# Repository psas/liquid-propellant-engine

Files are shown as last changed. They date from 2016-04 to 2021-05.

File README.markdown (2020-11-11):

# PSAS Liquid-Propellant Engine (LPE) Designs

## Overview

PSAS is building a LPE because (1) it's cool and (2) it's part of our 100 km rocket project. This project started with a 2015-2016 ME capstone of a 2kN 1/4 scale engine and is building towards a planned 9 kN engine for the LV-4 vehicle.

## Latest information

## 2020-2021 creation of the 2kN heat sink engine

Regenerative cooling is hard, particularly when we don't know if the basic engine design is viable. For this reason (and because we already bought some expensive parts), we are moving back to a ~2kN preliminary design. In various documents, this engine may be referred to as:

* 2kN Heat Sink Engine
* Minimum Viable Produce (MVP) engine
* Test Stand Demonstration Engine

The engine is intended to fire for no more than several seconds on the PSAS test stand. The hope is this engine will provide validation for the rocket design, manufacturing learnings and provide experience with a full-up hot fire test.

[Documentation for this engine](https://github.com/psas/liquid-propellant-engine/tree/master/2kN%20Heat%20Sink%20Engine)

## 2019-2020 Test Stand/Engine ME Capstone

Designed a 6kN heat sink engine... and then found out it was going to be too expensive to print and destroy this engine. Recommending moving back to 2kN for cost purposes.

[6kN Heat Sink Engine](https://github.com/psas/liquid-propellant-engine/tree/master/6kN%20Heat%20Sink%20Engine)

## 2018-2019 Test Stand Integration MME capstone

Project files analyzing and machining the 500lbf thrust printed engine.

Quick links to folders:
* [CT scanning](https://github.com/psas/liquid-propellant-engine/tree/master/2kN/CT%20scanning) <br>
* [Machining](https://github.com/psas/liquid-propellant-engine/tree/master/2kN/Machining)

## 2015-2016 liquid engine MME capstone.

Project files to develop a 500 lbf thrust 3D-printed liquid fuel rocket engine with LOX and IPA propellants. Here are a few helpful links:

* [Combustion chamber design Jupyter notebook](https://nbviewer.jupyter.org/github/psas/liquid-engine-capstone-2015/blob/master/2kN/analysis/Jupyter_Notebooks/LFRE.ipynb)
* [Pintle injector design Jupyter notebook](https://nbviewer.jupyter.org/github/psas/liquid-engine-capstone-2015/blob/master/2kN/analysis/Jupyter_Notebooks/Pintle%20Injector.ipynb)
* [Sketchfab 3D model of the Rev. 1 engine](https://sketchfab.com/models/ce8a3ff7d1e2417f9e614df5d085f7b0)
* [A short AIAA Space 2016 proceedings paper discussing the engine concept](https://github.com/psas/liquid-engine-capstone-2015/blob/master/2kN/doc/AIAA%20Space%20Proceedings/AIAA_Space_2016_Proceedings__LFRE_.pdf)
* [A short document explaning how the parametric curves for the cooling channels are computed](https://github.com/psas/liquid-engine-capstone-2015/blob/master/2kN/doc/Nozzle_Construction_docs/Cooling_Channel_Geometry_complete.pdf)

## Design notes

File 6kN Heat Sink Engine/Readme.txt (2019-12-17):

This is the location for 2019-2020 heat sink engine work.

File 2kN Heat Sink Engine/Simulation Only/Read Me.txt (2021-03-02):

This folder contains files that are to be used for optimizing the injector only. Dimensions may not match the current version. Dimensions that are directly relevant to the flow through the injector are the only parameters that should be updated to the current version.

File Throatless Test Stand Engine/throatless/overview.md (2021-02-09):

# Overview
This model is an estimated replica of Copenhagen Suborbital's BPM2. The model's dimensions are rough estimates from visually guessing BPM2's size in videos. The simulations were conducted with Solidworks Flow Sim. Inlet boundary conditions were gaseous H2O, 3000K, 250psi, with varying mass flow rates. Outlet boundary condition was environmental opening at 14.7psi and 293.15K temperature.

### My findngs

From Rocket Propulsion Elements by Sutton, Chapter 3.2:
> Chamber velocity can only be neglected if Ac/At > 4, only if chamber cross sectional area is 4 times bigger than throat area.

I believe that the losses from a throatless engine come from the immediate pressure loss in the chamber which is why the gas in the chamber is already accelerated and not stagnant like a traditional rocket engine. The high gas velocity right at the injector may be a result of the pressure loss, due to chamber and lack of throat geometry, which is being converted to velocity. 

Author: Kabir Bajwa

Date: February 9, 2021

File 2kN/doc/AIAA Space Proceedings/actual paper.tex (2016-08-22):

\typeout{}\typeout{If latex fails to find aiaa-tc, read the README file!}
%

\documentclass[]{aiaa-tc}% insert '[draft]' option to show overfull boxes
\usepackage{subfigure}
\usepackage{url}

 \title{Development of a Small Bipropellant Rocket Engine Utilizing Additive Manufacturing Processes}

 \author{
  John Tucker%
    \thanks{Student, Maseeh College of Engineering, AIAA Student Member.}
    \ Tamara Dib\thanksibid{1}\
  \ Taylor Rice\thanks{Student, Maseeh College of Engineering, AIAA Member}\ 
  \ Erin Schmidt\thanksibid{1}\
  \ Kristin Travis\thanksibid{1}\\
  \and
  \ and Bianca Viggiano%
   \thanks{Student, Maseeh College of Engineering.}\\
  {\normalsize\itshape
 Portland State University, Portland, OR, 97201, United States}
 }
 
 \AIAApapernumber{YEAR-NUMBER}
 \AIAAconference{AIAA SPACE 2016, 13-16 September 2016, Long Beach, California}
 \AIAAcopyright{\AIAAcopyrightD{2016}}

 % Define commands to assure consistent treatment throughout document
 \newcommand{\eqnref}[1]{(\ref{#1})}
 \newcommand{\class}[1]{\texttt{#1}}
 \newcommand{\package}[1]{\texttt{#1}}
 \newcommand{\file}[1]{\texttt{#1}}
 \newcommand{\BibTeX}{\textsc{Bib}\TeX}

\begin{document}

\maketitle

\begin{abstract}
The complexity and cost of building a liquid fuel rocket engine typically makes such devices unobtainable for a majority of parties interested in their construction. Until recently, manufacturing processes and techniques limited the geometries available to the designer and rendered such engines cost prohibitive as options for inexpensive orbital space flight. Advances in additive manufacturing technologies provide the potential to prototype complex geometries on a lower budget and with lead times which would be considered unobtainable with traditional manufacturing methods. Furthermore, bipropellant liquid fuels offer many complex engineering considerations; the full analysis of which may not be within the design ability of many amateur builds. It is therefore advantageous to develop techniques for additive manufacturing rapid prototyping to make the study of bipropellant fuels more accessible. A mechanical engineering senior capstone team at Portland State University developed an open-source method for quickly prototyping small bipropellant liquid fuel rocket engines with regenerative and film cooling using additive manufacturing.
\end{abstract}

\section*{Nomenclature} %keeping dummy variables for guidance

\begin{tabbing}
  XXXXX \= \kill% this line sets tab stop
  $PSAS$ \> Portland State Aerospace Society\\
  $DMLS$ \> Direct Metal Laser Sintering\\
  $LFRE$ \> Liquid Fuel Rocket Engine\\
  $LOX$ \> Liquid Oxygen\\
  $AM$ \> Additive Manufacturing\\
  $BF$ \> Blockage Factor\\
  $TMR$ \> Total Momentum Ratio\\
  
 % $\Delta x$ \> Variable displacement vector \\
 % $\alpha$ \> Acceleration, m/s\textsuperscript{2} \\[5pt]
 % \textit{Subscript}\\
 % $i$ \> Variable number \\
 \end{tabbing}

\section{Introduction}
The Portland State Aerospace Society (PSAS) is an engineering student group dedicated to low-cost, open-source technology development for high powered rockets and avionics systems \cite{PSAS}. The stated long term goal of the group is to place a 1 $kg$ CubeSat into low Earth orbit with their own launch vehicle. One step needed to achieve this goal is to transition the current rocket design from a solid to liquid fuel engine. Explored herein is the process of designing and testing a 500 $lbf$ thrust engine using liquid oxygen (LOX) and ethanol as propellants with regenerative cooling channels, film cooling, and a pintle injector. The design process is documented using Python in Jupyter notebooks and shared using Github \cite{git}. The authors feel that open standards for space systems hardware and design will be of increasing importance to the nascent `new space' industry. In this context, and in the interest of empowering `citizen scientists' and raising the level of public discussion on the issue of low-cost access to space the (non-ITAR controlled), project deliverables are being made freely and publicly available under a GNU GPL v3.0 open-source licence. 

A Jupyter Notebook is a sharable web application which allows for the live execution of code, namely Python. Jupyter notebooks were utilized in order to create a development process for the design of a regeneratively and film cooled liquid fuel rocket engine. The Jupyter Notebook forms a template for regeneratively cooled chamber design. As design inputs are changed in the notebook, parametric curves, which form the basis of the geometry file for 3D printing, are generated appropriately. This allows for quicker development of geometry files for additive manufacturing and thus quicker lead times on engine prototyping. As additive manufacturing technology progresses and becomes widely accepted by industry, its capability in rocket component design needs to be further studied and understood. Alloys used in Direct Metal Laser Sintering (DMLS) have different strength, heat transfer, and surface roughness properties. This project aims to gain insights on these properties and 3D printed combustion chamber performance. 

% it would appear we've covered everything without a top level design section, should we move things out of engine? or will this be sufficient?

%\section{Top Level Design}

\section{Engine}

%make the table a sub section? Also, i have zero clue about the style guide for a table, so I'm just going to construct it, with as much information as possible, we can cut or add anything we want, and style it all at once. I've commented out a lot of engine parameters, if you want to include them just uncomment them.

Engine design is typically cost prohibitive for many amateur designers who may be able to contribute to the advancement of low cost orbital space flight. The design process is cumbersome, and oftentimes does not result in a final product that will successfully fire due to the complexity of engine design. Engineering tools are not generally available, and an understanding of the full process is lacking. Due to the aforementioned constraints, it is desirable for the amateur to have available a design tool which will aid in generating a geometry capable of withstanding the stresses of a steady-state engine, while simultaneously producing a desired thrust. A production engine was generated and built using the Jupyter Notebook. Table \ref{tab:engineparams} shows a variety of the theoretical engine parameters generated by the liquid fuel rocket engine (LFRE) notebook.

\begin{table}
\begin{center}
\begin{tabular}{| l | c | c |}

\hline
 Parameter, variable                      & Unit     & Value     \\
 \hline
 Nozzle force, $F$                        & $lbf$       & 500       \\
 O/F weight mixture ratio, $r_w$          & --  & 1.2       \\
 Fuel mixture percentage, $r_{w_{fuel}}$  & --   & 0.595      \\
 Contraction ratio, $\varepsilon_c$       & --  & 10.5      \\
 Ratio of specific heats, $\gamma$        & --  & 1.12      \\

 %Pressures:
 Total chamber pressure, $P_{c_{inj}}$    & $psi$  & 350.00    \\
 Throat pressure, $P_t$                   & $psi$       & 202.73    \\

 %Velocities:
 Throat velocity, $V_t$                   & ${ft}/{s}$    & 3464.05   \\
 Exit velocity, $V_e$                     & ${ft}/{s}$    & 7804.45   \\

 %Mass Flow Rates:
 Total mass flow rate, $\dot w$           & ${lb}/{s}$    & 2.06      \\

 %Temperatures:
 Stagnation temperature, $T_{c_{ns}}$             & $^\circ R$ & 5487.10   \\
 Adiabatic wall temperature at inlet, $T_{awi}$   & $^\circ R$ & 4389.64   \\
 Adiabatic wall temperature at throat, $T_{awt}$  & $^\circ R$ & 4379.47   \\

 Specific Impulse, $I_s $                 & ${lb\cdot s}/{lb}$    & 242.37    \\
 Characteristic velocity, $c*$            & ${ft}/{s}$            & 5325.59   \\

 Chamber volume, $V_c$                    & $in^3$      & 27.35     \\
 Chamber cross sectional area, $A_c$      & $in^2$      & 10.26     \\
 Throat radius, $r_t$                     & $in$        & 0.558     \\
 Exit radius, $r_e$                       & $in$        & 1.037     \\
 Wall thickness, $t$                      & $in$        & 0.01820   \\
 
 Cooling channel base width at throat, $b_t$              & $in$        & 0.02522   \\
 Cooling channel base width at exit, $b_e$                & $in$        & 0.06192   \\
 Cooling channel effective radius at throat, $r_{cch_t}$  & $in$        & 0.01261   \\
 Cooling channel effective radius at exit, $r_{cch_e}$    & $in$        & 0.03096   \\
 Cooling channel hydraulic diameter, $d$                  & $in$        & 0.04671   \\
 Cooling channel total area, $A_c$                        & $in^2$      & 1.16537   \\
 Number of cooling channels, $n$                          & --  & 82        \\

 Coolant side heat transfer coefficient, $h_c$    & ${Btu}/({in^2\cdot s\cdot^{\circ}F})$   & 0.15609   \\
 Required heat flux, $\dot q$                          & ${Btu}/({in^2\cdot s})$                 & 27.72     \\
 Coolant capacity, $Q_c$                          & ${Btu}/{s}$                           & 341.68    \\
 
 Combined tangential stress at nozzle exit, $S_{t_e}$     & $psi$       & 32224.43  \\
 Combined tangential stress at throat, $S_{t_t}$          & $psi$       & 31554.40  \\
\hline
\end{tabular}
\end{center}
\caption{Parameters obtained from the Jupyter Notebook for the production engine chamber and nozzle design.}
\label{tab:engineparams}
\end{table}

The LFRE Nozzle Jupyter Notebook \cite{LFRE} allows the user to input desired design requirements; namely thrust and material properties, to subsequently aid the designer in generating an acceptable geometry for the specified requirements. NASA's CEARUN tool \cite{CEARUN} is used to generate many of the initial design parameters as inputs. Certain design constraints (fuel combination, mixture ratio, and chamber pressure) must be known prior to utilizing the CEARUN tool, and should be selected according to needs of the engine design. After inputs are provided, the basic geometry of the nozzle is determined. Furthermore, the analysis determines the cooling capacity of the fuel used in regenerative passages resulting in parametric equations which describe the chamber and nozzle contours, the inner and outer surfaces of the regenerative cooling passages, and the external surface of the nozzle. The parametric equations may then be used to generate a printable 3D model in combination with additive manufacturing processes.

The regenerative cooling passages constructed using the parametric equations are of uniform cross-sectional area normal to the surface of the nozzle contour. These parametric equations were derived in order to mathematically define a nozzle contour and its various cooling channel geometries in general such that no geometry would have to be calculated by the designer, and a nozzle could be generated by virtue of only the geometric parameters which make it unique \cite{parametricEQs}. Full development of the parametric equations are available for inspection, but are not provided here for the sake of brevity. This allows the  cross sectional area to be scaled as a means of controlling the velocity of the fuel in a particular regenerative passageway, enabling better control of wall temperatures at any given axial position along the nozzle. Scaling functions may be added as a design tool at a later date, but initial functions resemble a half period of a sine function to scale along a desired length of nozzle in order to give a smooth and continuous scaling pattern along a given section of the nozzle. Because the nozzle is parametrized, any parametric equation justifying a nozzle section may simply be multiplied by a scaling function in order to more directly control cooling over specific areas of the nozzle.
 
After generating parametric equations, a more detailed heat transfer analysis is undertaken. Properties are evaluated along finite sections of the wall contour, and compared to the capacity of the specified coolant, to allow the designer to analyze if a particular nozzle geometry is capable of reaching a thermal equilibrium while remaining below the thermal and mechanical stress limits of the engine material and the boiling point of the fluid. The analysis generates graphs of several key properties along the nozzle contour as shown in figure \ref{fig:propertygraphs}. The major outputs of the Jupyter Notebook are a unique set of parametric equations with which a liquid fuel rocket engine is created which utilizes regenerative and film cooling to protect the engine material from yield due to thermal and mechanical stresses during thermally steady state combustion.

%\begin{figure}[h]
%\centering
%   {\includegraphics[width=.3\textwidth]{graphs/radius_v_position.png}
%    \includegraphics[width=.3\textwidth]{graphs/mach_v_position.png}
%    \includegraphics[width=.3\textwidth]{graphs/pressure_v_position.png}
%    \includegraphics[width=.3\textwidth]{graphs/temp_v_position.png}
 %   \includegraphics[width=.3\textwidth]{graphs/velocity_v_position.png}
 %   \includegraphics[width=.3\textwidth]{graphs/HT_coeff_v_position.png}
 %   \includegraphics[width=.3\textwidth]{graphs/adiab_wall_temp_v_position.png%}
 %   \includegraphics[width=.3\textwidth]{graphs/heat_flux_v_position.png}}
 %   \caption{LFRE Jupyter Notebook sample output for various properties along the length of the developed nozzle}
 %%   \label{fig:propertygraphs}
%\end{figure}

\begin{figure}[ht]
\centering
   {
    
    }
    \caption{LFRE Jupyter Notebook sample output for Mach number, temperature and heat flux along the length of the developed nozzle. For a complete set of parameters plotted as a function of nozzle position see the Github repo \cite{LFRE}.}
    \label{fig:propertygraphs}
\end{figure}

Correction factors are implemented into the Jupyter Notebook to address discrepancies between theoretical values for various parameters and their empirically tested values. The primary correction factor to be addressed after testing an engineering prototype should be the adiabatic wall temperature of the hot exhaust gas due to film cooling. Models for film cooling are not well established, and it is important to determine a correction factor for a particular engine in order to accurately predict the resulting physical properties of subsequent iterations of engine prototypes. This will allow a designer to predict the flow rates and pressure drops of propellants with enough accuracy to design a propellant feed system capable of delivering required pressure to an engine without the need to iterate through many costly test stand designs.

\subsection*{Engine Features}

The first engine prototype shown in figure \ref{fig:nozzlecross} is intended to produce 500 $lbf$. It is produced by a DMLS 3D printing process and made from high temperature aluminum alloy, AlSI10Mg. External to this project, a test stand  is being built that is capable of delivering fuel at approximately 500 $psi$ to the fuel manifold, which is located at the base of the nozzle bell. Upon collection, the fuel is directed through regenerative cooling channels. The fuel is then delivered to a collection chamber. Care should be taken to limit the overhang angles within the larger geometries of the collection chamber. This limit is dictated by the particular 3D printing process which is being utilized. The designer should consider the print orientation and maximum overhang angle. The presented prototype was printed with a maximum overhang angle of 45$^\circ$, and the design resulted in minimal use of support material. Upon collection, the fuel is directed to film cooling ports, shown in figure \ref{fig:designcross}; of which the size and quantity are optimized by the Jupyter Notebook. Remaining fuel is then utilized as propellant, which is directed around a pintle injector, described in section \ref{sec:PI}. After injection and combustion occur, the propellants are directed through a de Laval nozzle design based on Rao's parabolic bell approximation \cite{rao1961recent}.

\begin{figure}[ht]
\centering
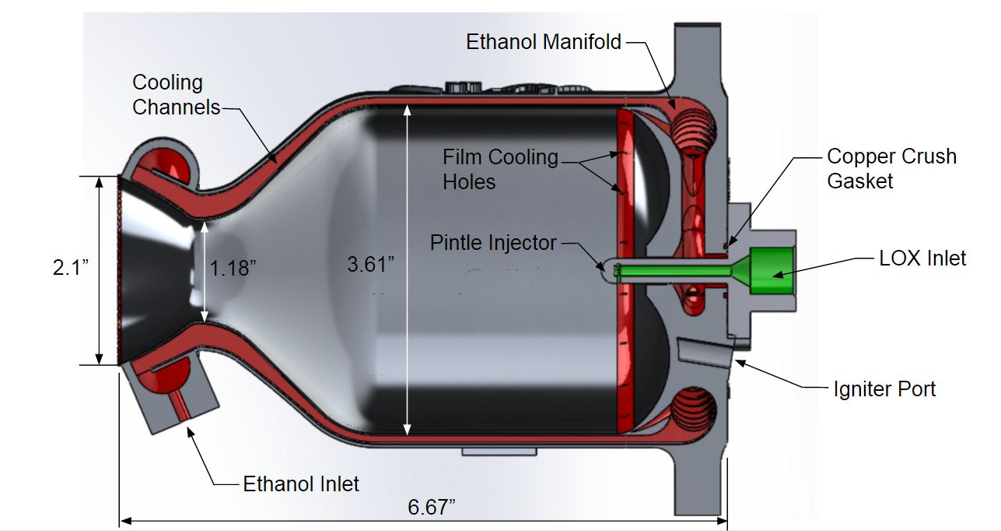
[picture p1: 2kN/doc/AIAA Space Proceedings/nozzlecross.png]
   {}
    \caption{Final assembly cross section drawing of the rocket engine. Areas in red show the regenerative cooling channels and the path the fuel takes through the engine. Areas in green are the liquid oxygen flow path.}
    \label{fig:nozzlecross}
\end{figure}

\begin{figure}[ht!]
\centering
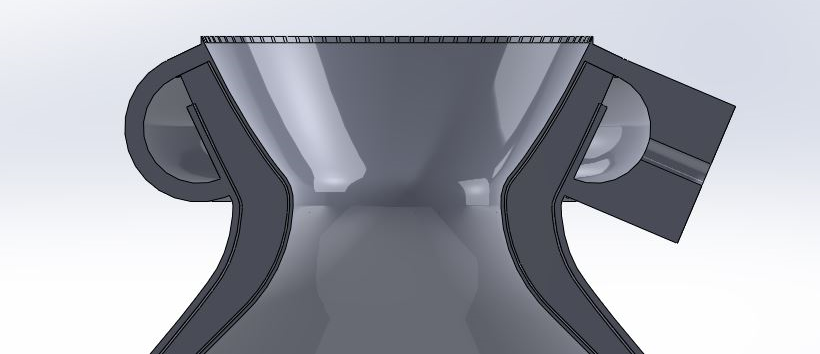
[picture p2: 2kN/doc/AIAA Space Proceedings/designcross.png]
    {}
    \caption{Final design cross section drawing of the nozzle bell, the nozzle and fuel manifolds are manufactured as a single part. The nozzle is a parabolic approximation of a de Laval converging-diverging nozzle.}
    \label{fig:designcross}
\end{figure}

DMLS uses high energy pulse CO2 lasers (carbon dioxide laser) to fuse metal particles together, layer-by-layer, to form a solid product. The process is done in a powder bed that inherently provides support material for any overhanging features. Because of this, complex features and internal passageways are possible utilizing DMLS that are not possible with traditional machining approaches. Incorporating DMLS manufacturing allows the designer to work towards the 'ideal' design for a rocket engine without the added burden of considering machinability. Features such as regenerative cooling channels no longer require special machining strategies for incorporation into a design. They are instead printed directly into the nozzle contours simply and accurately with only feature size and overhang angles as constraints. 

\section{Pintle Injector}
\label{sec:PI}

%The pintle section needs a stats table, similar to the engine stats table. 
%Here it is, but it needs formatting

There are several possibilities for the selection of the injector.
%This sentence doesn't make sense to me. Are 'stable and efficient manners' performance characteristics? Which performance characteristics?
%Most injector types are capable of atomizing the fuel in a stable and efficient manner, therefore performance characteristics are not the driving factor in design selection.
A 500 $lbf$ thrust engine has low fuel mixing requirements; as long as the mass flow rates and momentum ratios are satisfied, many different designs will suffice. Swirl injectors, as well as impinging jet injectors were considered; however, these designs are more complex and potentially more difficult to integrate with 3D printed cooling channels. As a result, an interchangeable pintle injector design based on 
research published by Santoro was selected \cite{santoro1999main}. A pintle injector will be fixed to the engine via bolts or machine screws, making it relatively easy to remove and replace if alterations are necessary. Additionally, pintle injectors are less susceptible to combustion instabilities  and are potentially throttle-able; features that will benefit future PSAS liquid engine designs\cite{dressler2000trw}. 
%is it ok that I changed 'larger' to 'PSAS liquid'?

The pintle injector is responsible for delivering the liquid oxygen to the combustion chamber. 316 stainless steel was chosen as the pintle injector material because of its LOX compatibility and thermal resistance qualities. The liquid oxygen travels down the center of the pintle and leaves the LOX holes at a 90$^\circ$ angle to the original direction of travel. The liquid oxygen exiting the pintle holes collides with the annulus fuel stream and creates an atomized mixture. The oxygen holes and fuel gap have been sized to achieve near equal flow momentum of each propellant resulting in a TMR near unity to ensure the trajectory of the mixture inside the combustion chamber is $\sim$45$^\circ$. The design for the pintle injector is shown in figure \ref{fig:PIxsection}.

\begin{figure}
\centering
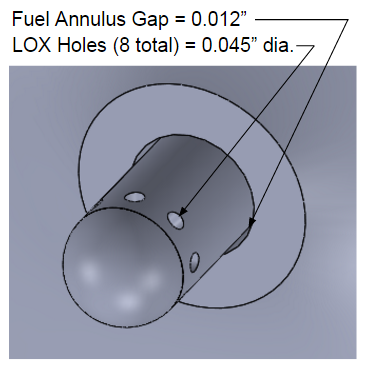
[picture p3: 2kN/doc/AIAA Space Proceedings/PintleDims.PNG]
   \subfigure[]{}
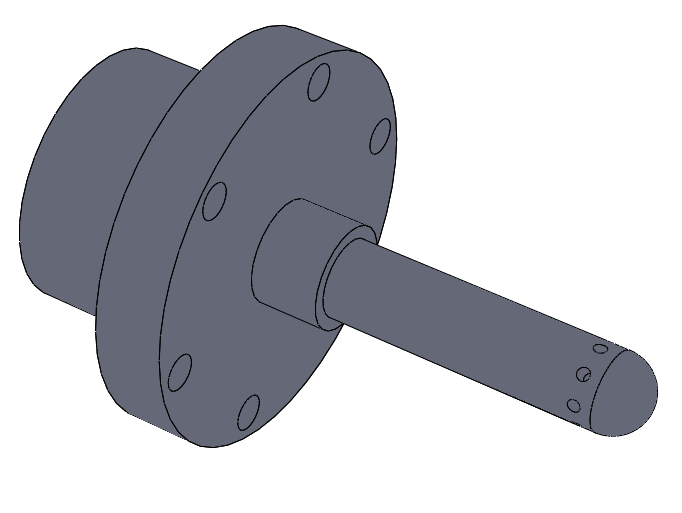
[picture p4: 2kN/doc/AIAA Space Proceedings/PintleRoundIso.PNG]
   \subfigure[]{}
    \caption{Pintle LOX holes and fuel annulus inside combustion chamber (a) and Stainless Steel pintle injector design (b).}
    \label{fig:PIxsection}
\end{figure}

Currently there is little published data on the design and construction of pintle injectors. Therefore an extensive documentation of the design process has been outlined in the Github repository. Using the Jupyter Notebook in Github, radii for the LOX holes and the fuel annulus were determined from inputs for required chamber pressure and propellant mass flow rates. The dimensions of the radii can be adjusted according to recommended blockage factor (BF) and total momentum ratio (TMR) values provided by Woodward \cite{woodward1998injector}. The notebook is constructed for ease in calculations for an iterative process. Table \ref{tab:pintle} shows the theoretical parameters generated by the Jupyter Notebook that pertain to the design of the current pintle injector.

\begin{table}
\begin{center}
\begin{tabular}{| l | c | c |}
\hline
 Parameter, variable                          & Unit     & Value     \\
  \hline
  Pintle center LOX flow rate, $\dot w_{ox}$                                  & ${lb}/{s}$       & 1.13       \\
   Outer annulus ethanol flow rate, $\dot w_f$
   & ${lb}/{s}$       & 0.94       \\
 Pintle outer radius, $R_p$                              & $in$       & 0.14       \\
 Pintle inner radius, $r$          
 & $in$   & 0.06       \\
Fuel annulus radius, $R_a$          
 & $in$   & 0.152       \\
 Annulus gap, $t$          
 & $in$   & 0.012       \\
 Injector pressure drop, $\Delta P$          
 & $psi$   & 70       \\
  Pintle hole diameter, $d_h$          
 & $in$   & 0.045       \\
   Number of pintle LOX holes, $N$         
 & --   & 8       \\
  Theoretical Blockage Factor, $BF$          
 & --   & 0.41       \\
   Theoretical Total Momentum Ratio, $TMR$          
 & --   & 0.97       \\  
\hline
\end{tabular}
\end{center}
\caption{Parameters obtained from the Jupyter Notebook for the current pintle injector design.}
\label{tab:pintle}

\end{table}

\section{Ongoing and Future Work}
All entities of the printed production engine, shown in figure \ref{fig:IMG_1371}, must still be tested, including the injector and nozzle. The regenerative cooling channels of the nozzle will be cold flow tested prior to any hot fires. The pintle injector has been designed and is in the midst of being machined; it will be cold flow tested prior to being attached to the nozzle. The ignition system is currently being designed as well as the instrumentation to test fire the engine.%'engine' used to be 'rocket'. 

\begin{figure}[ht!]
\centering
    {}
    \caption{Printed engine to be cold tested and hot fired.}
    \label{fig:IMG_1371}
\end{figure}

A future iteration of the Jupyter Notebook would include constant hydraulic diameter as an output rather than a constant cross sectional area, in order to give the designer a unit flow velocity along the channels. The flow velocity could then be scaled as desired around areas of high heat transfer such as the throat.

\section{Conclusion} %I am adddding a sentence here.
To the knowledge of the authors, no other open-source method for quickly prototyping liquid fuel engines exists. The first iteration of this engine will be tested on a test stand in 2016. The results obtained from the cold tests and hot fire of the engine will aid in future iterations and give insight into the validity of the equations utilized for this engine. 3D printed engines are just beginning to be developed and tested by industry, and few have been tested in flight. Additive manufacturing has opened the door for design innovation, low cost development, and amateur group access to space.

%\section*{Appendix}
%should we include links to things like the derivations of contour equations, or the various Jupyter notebooks?

\section*{Acknowledgments}
The authors are grateful to PSAS for funding and initiating this project, Faculty Advisor Dr. Derek Tretheway for his advice and guidance and Cam Yun for his work on the project. The authors are also grateful to Robert Watzlavick, David Gregory, and Armor Harris for their advice, and the Oregon Air National Guard for their guidance on LOX handling. Finally the authors are indebted to i3D MFG for their ongoing support with additive manufacturing and Machine Sciences Corporation for their support with traditional machining.

\bibliography{aiaabib}
\bibliographystyle{aiaa}

\end{document}

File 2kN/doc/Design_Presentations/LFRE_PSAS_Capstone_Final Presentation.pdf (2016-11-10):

# Liquid Fuel Rocket Engine

## Portland State Aerospace Society Senior Capstone Project

Tamara Dib, Taylor Rice, Kristin Travis,

## John Tucker, Bianca Viggiano, Cam Yun Faculty Advisor: Derek Tretheway

# Portland State Aerospace Society (PSAS)

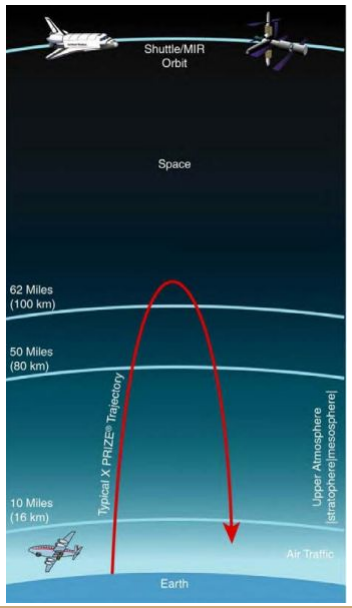
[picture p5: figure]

-University Space Race - The Von Karman Line (100km)

-Last Launch Altitude ~5km

-Transition from solid motor to liquid fuel engine to reach 100km

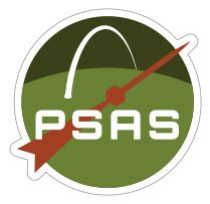
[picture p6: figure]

-Open Source - Github

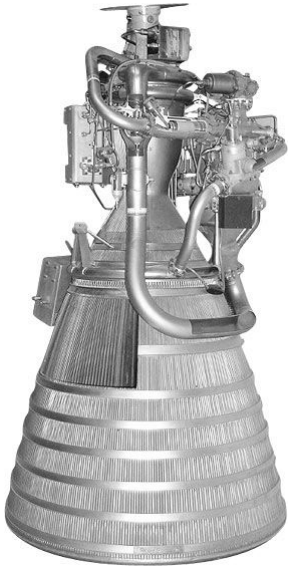
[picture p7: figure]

# Original Design Criteria

-Design, build and test a prototype static liquid fuel rocket engine with 50 lbf thrust capability

-Use DMLS additive manufacturing technology (3D-Print Direct Metal Laser Sintering)

-Scalable proof of concept design for future engine design iterations

-Develop and document engine design process to provide open source ‘templates’ for future engine designs

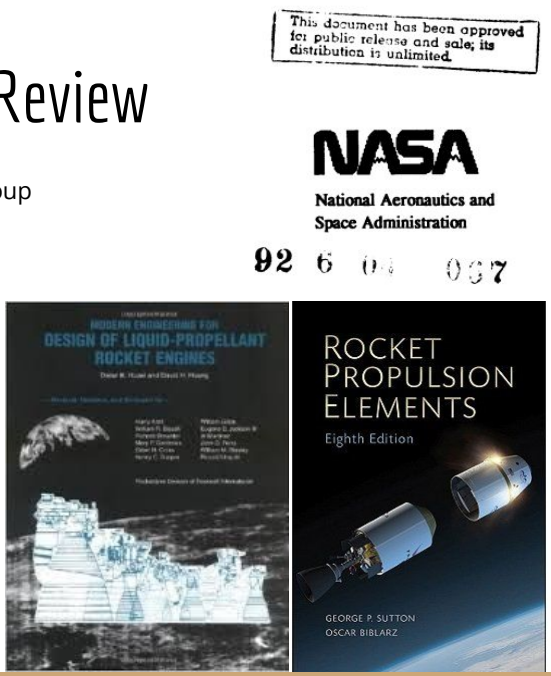
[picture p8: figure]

# External Search and Design Review

-Armor Harris - SpaceX and Boston University Rocket Group

-Robert Watzlavick - Aerospace Engineer

-Peter McCloud - Aerospace Engineer

-Oregon Air National Guard - LOX handling

-NASA and AIAA Publications

-aRocket - Amateur rocketry email list

-Reddit - Rocketry Thread

-Erin Schmidt - PSAS

# Current Engine Design

-500 lb Thrust

-Static test stand engine

-3D printed in Aluminum (AlSi10Mg)

-Ethanol and Liquid Oxygen (LOX) Propellants

-Fuel filled regenerative cooling channels

-Film cooling ports

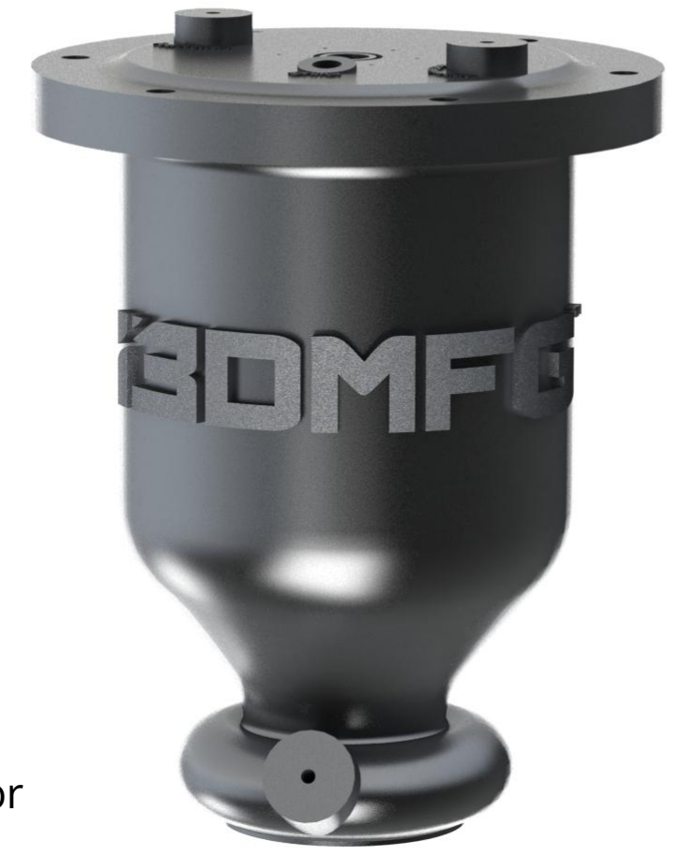
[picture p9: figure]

-LOX centered 316 stainless steel pintle injector

# Current Engine Design

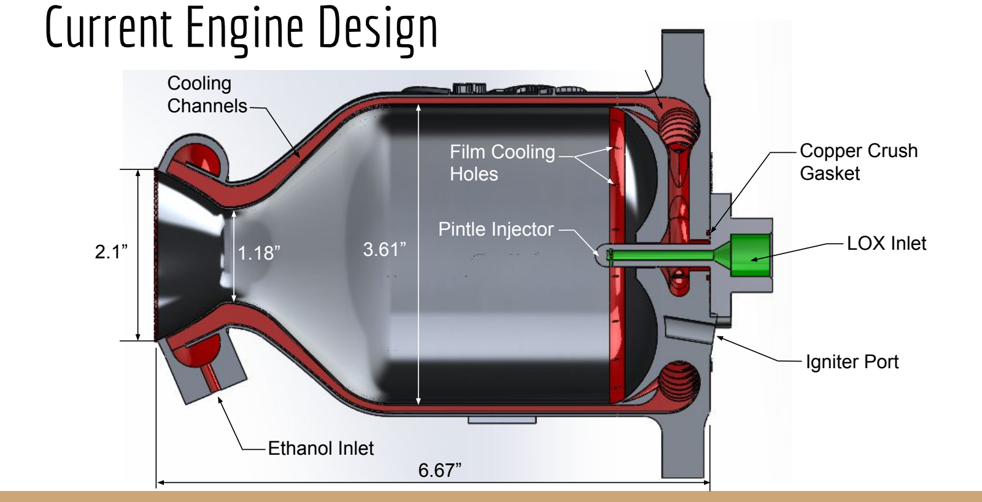
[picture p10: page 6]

Ethanol Inlet

Cooling
Channels

Ethanol Manifold

LOX Inlet

Copper Crush
Gasket

Pintle Injector
2.1” | 1.18” | 3.61”

6.67”

Film Cooling
Holes

Igniter Port

# Regenerative Cooling Channels

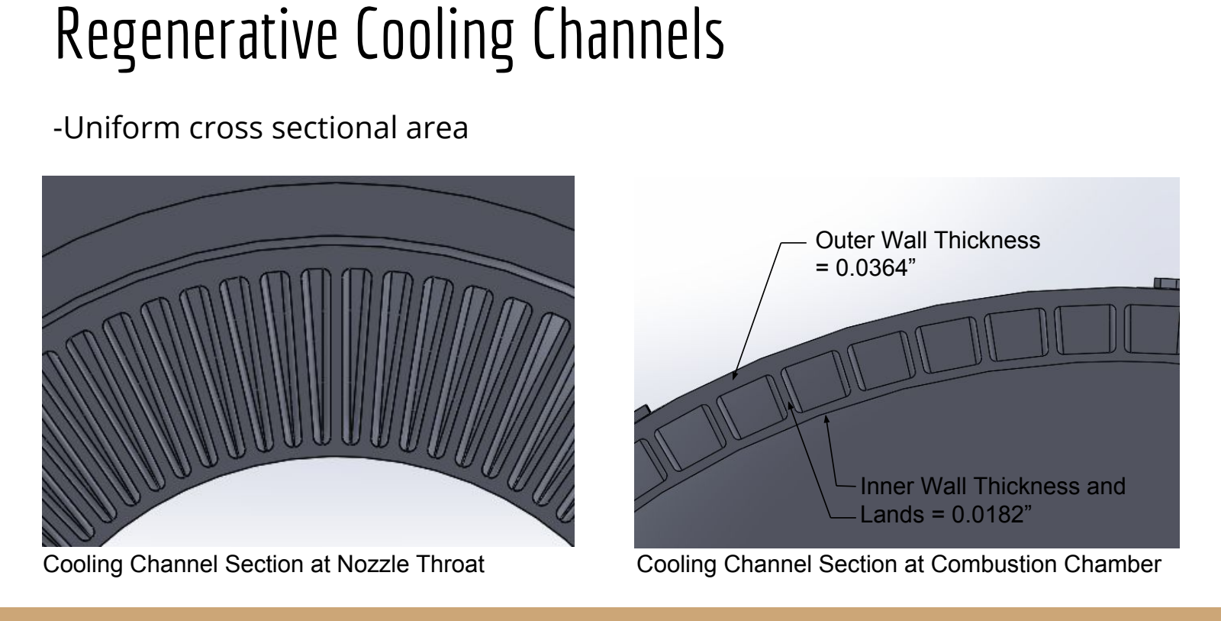
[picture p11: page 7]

Cooling Channel Section at Nozzle Throat | Cooling Channel Section at Combustion Chamber

-Uniform cross sectional area

Outer Wall Thickness
= 0.0364”

Inner Wall Thickness and
Lands = 0.0182”

# Heat Transfer Analysis and Film Cooling

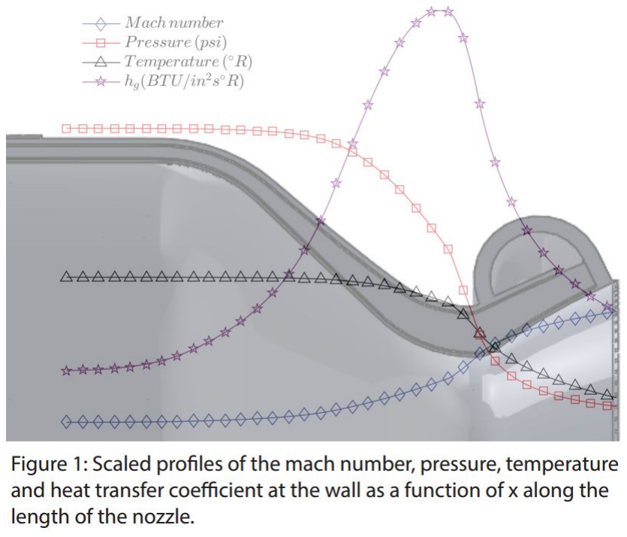
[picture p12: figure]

-Balance between thermal stresses
and print resolution

-Flow temperatures approaching 2,782 °C (5,500 °R)

# Open Source Jupyter (ipython) Design Notebooks

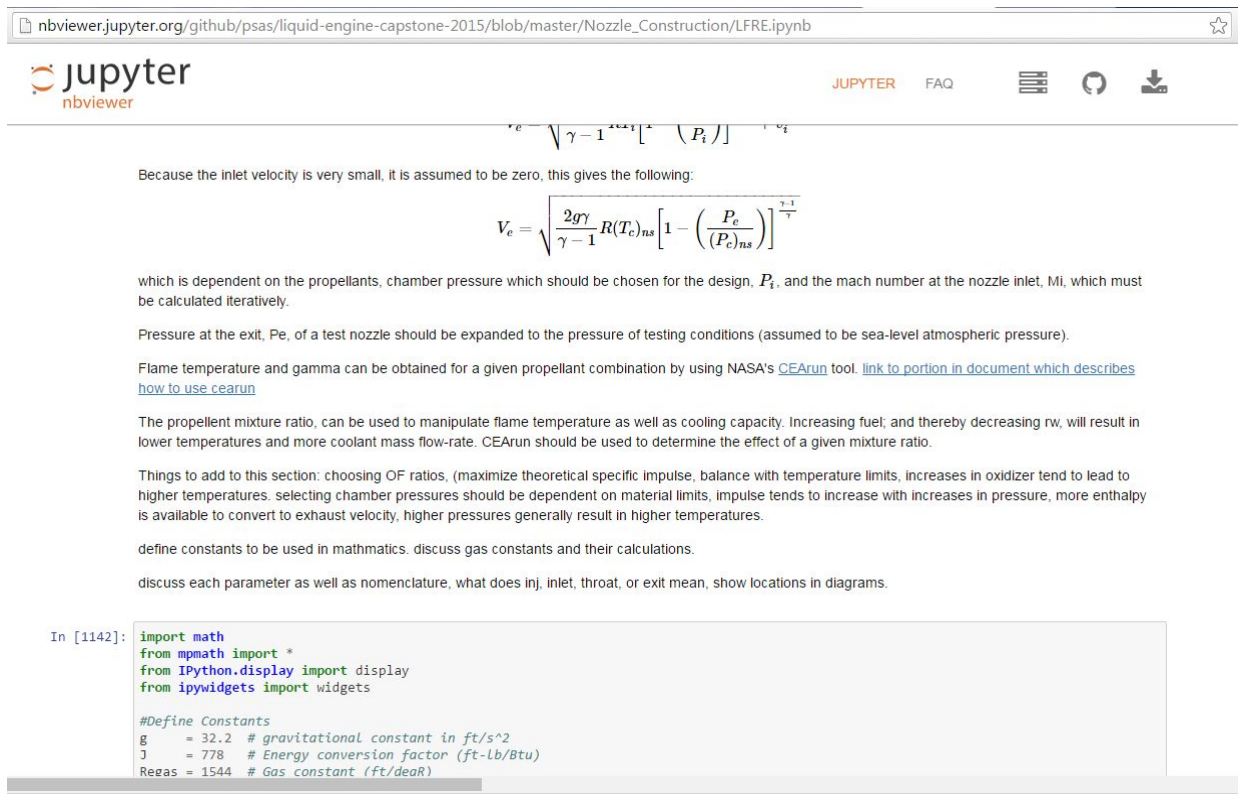
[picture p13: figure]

# Pintle Injectors

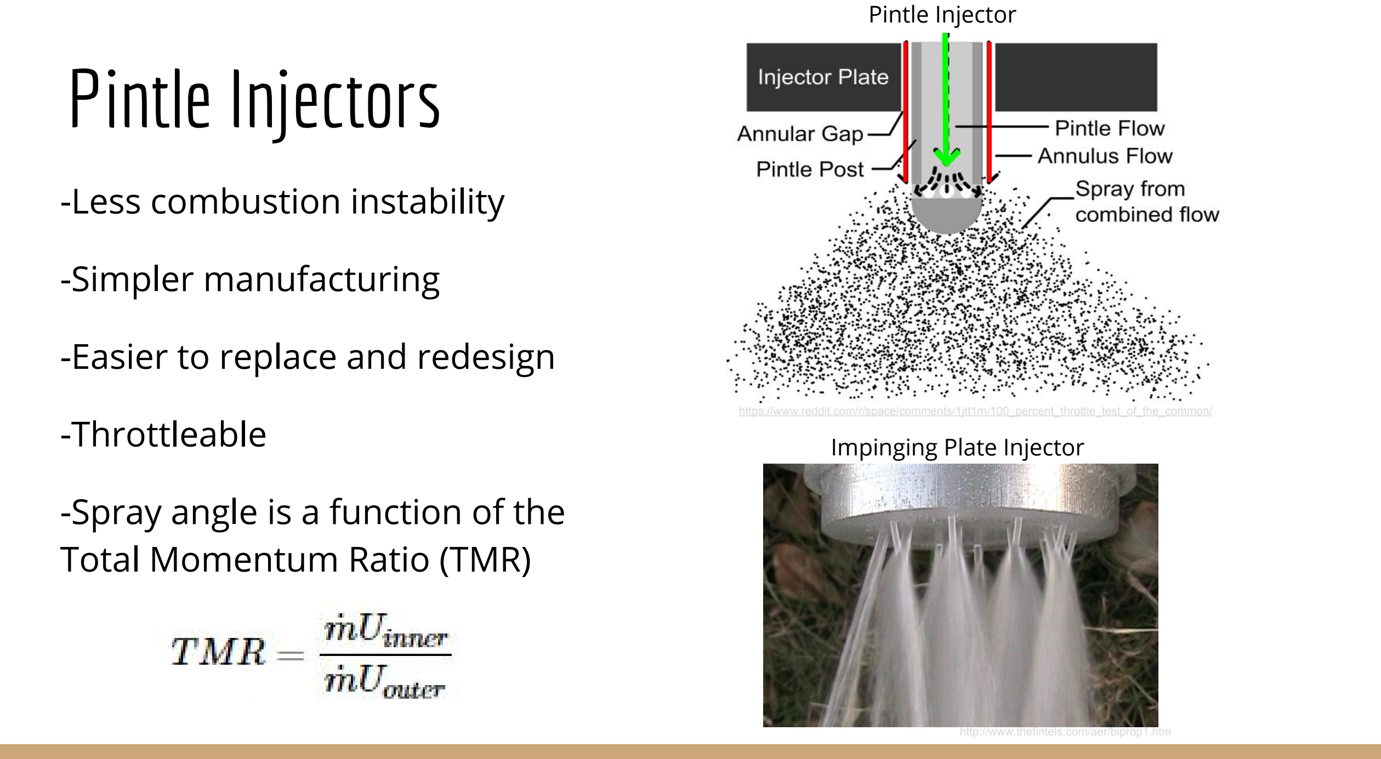
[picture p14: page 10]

-Less combustion instability

-Simpler manufacturing

-Easier to replace and redesign

-Throttleable

-Spray angle is a function of the Total Momentum Ratio (TMR)

Impinging Plate Injector

Pintle Injector

http://www.thefintels.com/aer/biprop1.htmhttps://www.reddit.com/r/space/comments/1jtt1m/100_percent_throttle_test_of_the_common/

# Pintle Injector Design

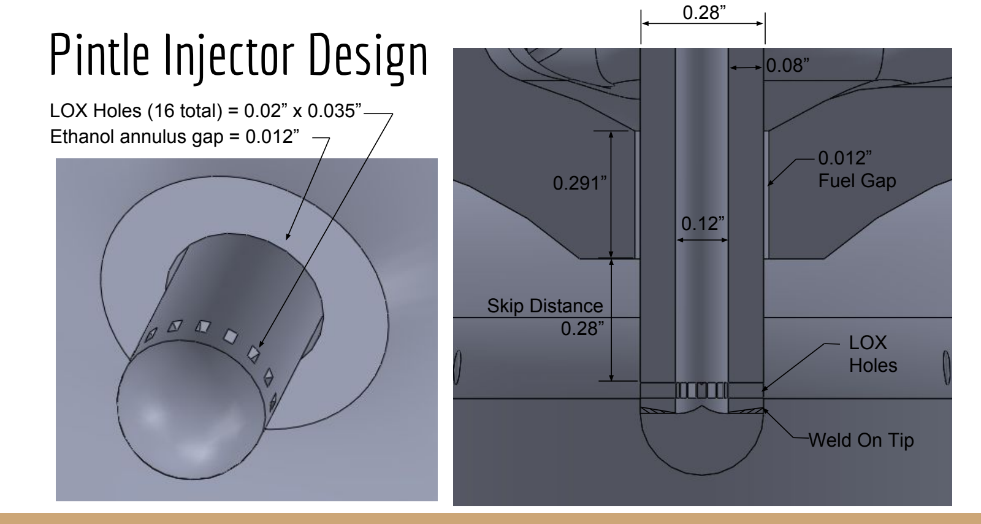
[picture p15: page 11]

0.28”

LOX Holes (16 total) = 0.02” x 0.035” Ethanol annulus gap = 0.012”

LOX
Holes

0.12”

Weld On Tip

0.291”

Skip Distance
0.28”

0.012”
Fuel Gap

0.08”

# Pintle Injector Design

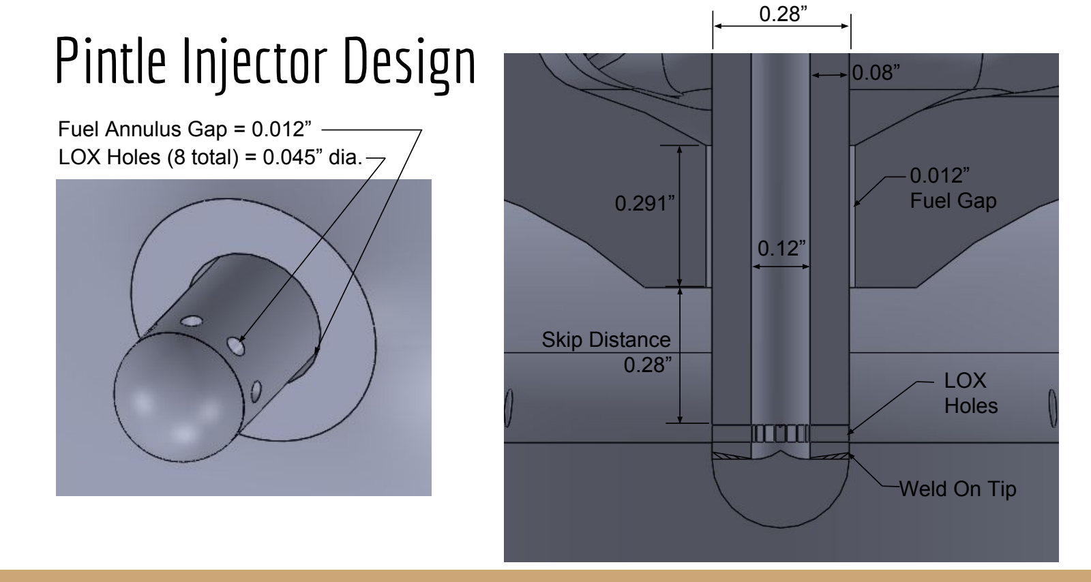
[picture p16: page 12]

0.28”

LOX Holes (8 total) = 0.045” dia.

Fuel Annulus Gap = 0.012”

LOX
Holes

0.12”

Weld On Tip

0.291”

Skip Distance
0.28”

0.012”
Fuel Gap

0.08”

# Torch Spark Igniter

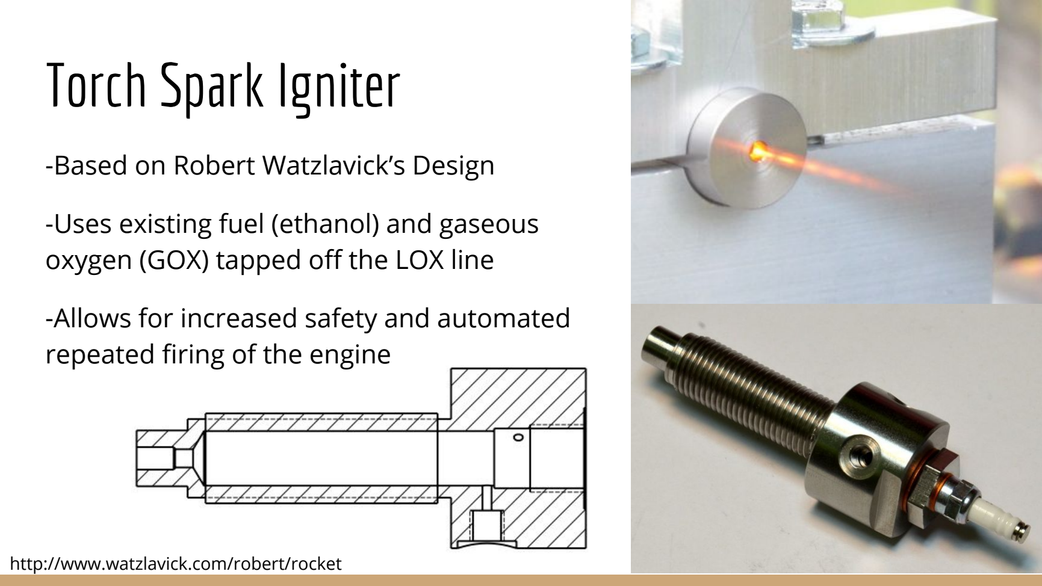
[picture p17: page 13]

-Based on Robert Watzlavick’s Design

-Uses existing fuel (ethanol) and gaseous oxygen (GOX) tapped off the LOX line

-Allows for increased safety and automated repeated firing of the engine

http://www.watzlavick.com/robert/rocket

# Liquid Oxygen (LOX) Handling

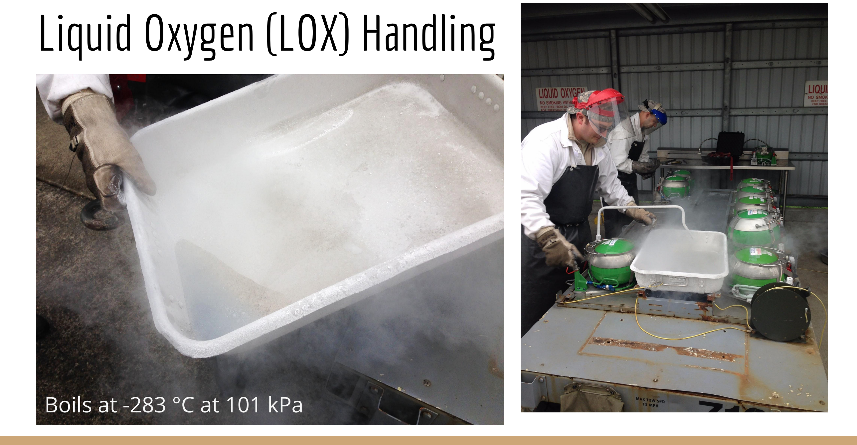
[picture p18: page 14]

Boils at -283 °C at 101 kPa

# Cool Images!

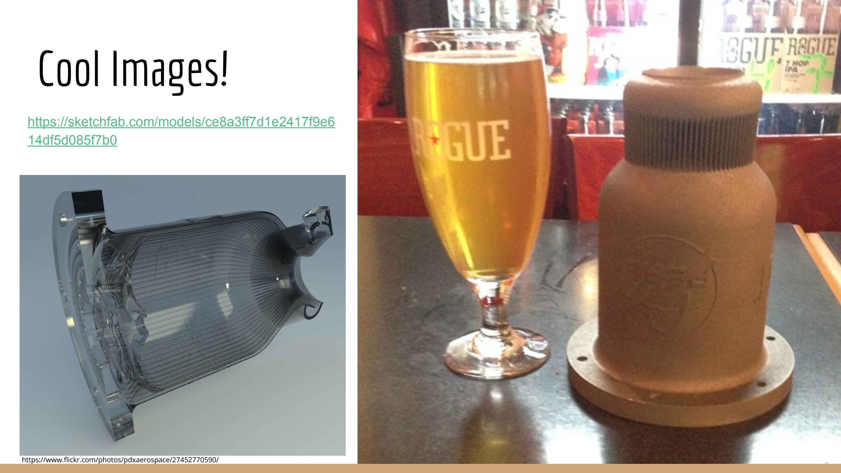
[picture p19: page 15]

https://sketchfab.com/models/ce8a3ff7d1e2417f9e6 14df5d085f7b0 (https://sketchfab.com/models/ce8a3ff7d1e2417f9e614df5d085f7b0)

https://www.flickr.com/photos/pdxaerospace/27452770590/

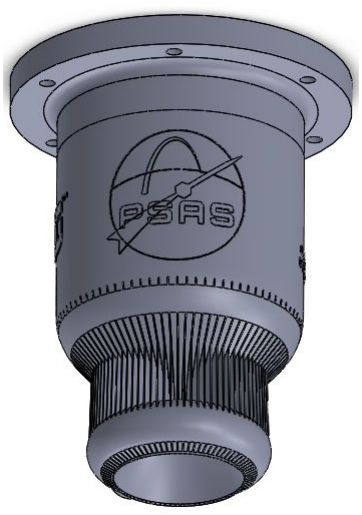
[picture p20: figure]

# Ongoing Projects

-Manufacture injector

-Cold flow test injector

-Test pressure loss in cooling channels

-Manufacture and test igniter

-FEA and CFD model validation

-Fire the Engine!

# Questions?

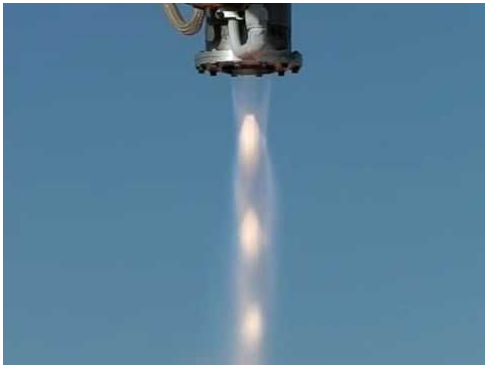
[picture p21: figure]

Thank you to all our supporters!

-i3D Manufacturing
-Portland State Aerospace Society -Derek Tretheway
-Andrew Greenberg
-Armor Harris
-Robert Watzlavick
-Peter McCloud
-Erin Schmidt

# Image References

http://psas.pdx.edu/
http://www.mrziegler.com/images/XPrizeTrajectory.jpghttps://www.asme.org/about-asme/who-we-are/engineering-history/landmarks/36-rl-10-rocket-enginehttp://i.imgur.com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
http://www.thefintels.com/aer/biprop1.htm
http://www.watzlavick.com/robert/rockethttps://www.flickr.com/photos/pdxaerospace/27452770590/https://i.ytimg.com/vi/KeGidtk6t2Y/hqdefault.jpg

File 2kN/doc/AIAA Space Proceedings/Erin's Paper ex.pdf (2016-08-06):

# Development of a Low-Cost, Open-Hardware Attitude Control System for High Powered

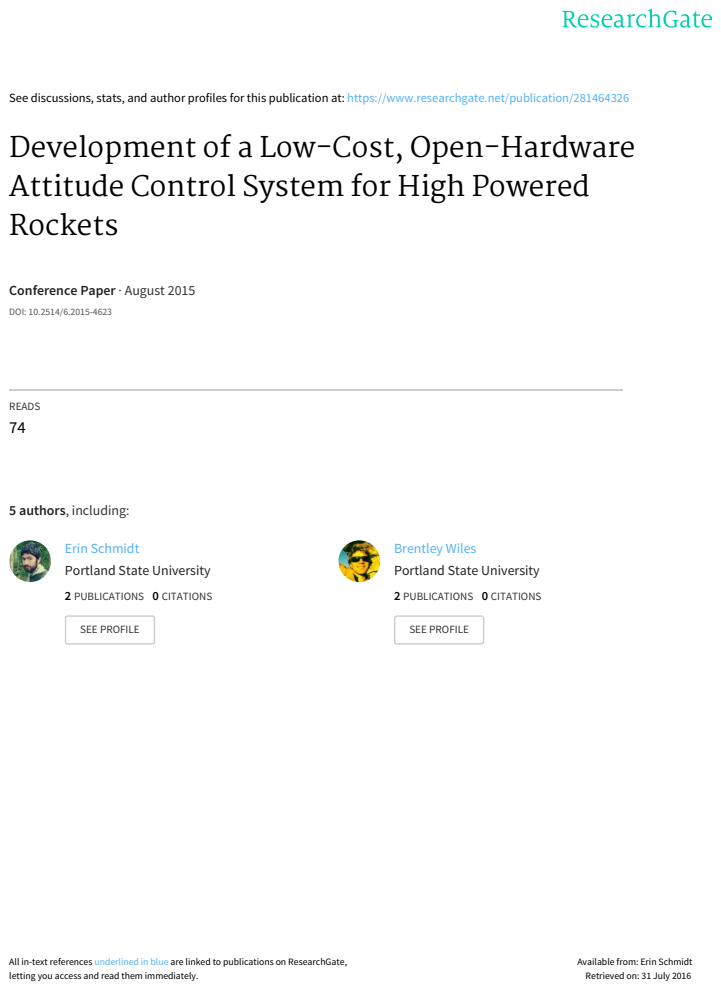
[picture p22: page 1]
Rockets; DOI: 10.2514/6.2015-4623; READS 74; 5 authors, including:; 2 PUBLICATIONS 0 CITATIONS; SEE PROFILE

See discussions, stats, and author profiles for this publication at: https://www.researchgate.net/publication/281464326

Conference Paper · August 2015

Erin Schmidt (https://www.researchgate.net/profile/Erin_Schmidt3?el=1_x_5)
Portland State University (https://www.researchgate.net/institution/Portland_State_University?el=1_x_6)

Brentley Wiles (https://www.researchgate.net/profile/Brentley_Wiles?el=1_x_5)

All in-text references underlined in blue are linked to publications on ResearchGate,
letting you access and read them immediately.

Available from: Erin Schmidt
Retrieved on: 31 July 2016

1 Student, Maseeh College of Engineering, Student Member 2 Student, Maseeh College of Engineering, Student Member 3 Student, Maseeh College of Engineering
4 Student, Maseeh College of Engineering, Student Member 5 Student, Maseeh College of Engineering, Student Member

American Institute of Aeronautics and Astronautics

# Development of a Low-Cost, Open-Hardware Attitude Control System for High-Powered Rockets

Erin Schmidt¹

, Jeremy Louke²

, Kenneth Arnell³

, Jeffrey Hickman⁴

, and Brentley Wiles⁵
Portland State University, Portland, OR 97201

Attitude control systems are an important enabling technology for amatuer and university class high-powered rockets to be more useful as platforms for high-altitude science, but are presently too costly and technically complex to implement for many groups. With the intention of making this technology more accessible to the high-powered rocketry field a mechanical engineering senior capstone team at Portland State University developed an open-source, scalable attitude control system leveraging COTS components, robust controls, and additive manufacturing. A qualitative narrative describing the system design process is presented here.

Nomenclature
COTS = Commercial Off The Shelf
DoF = Degree of Freedom
IMU = Inertial Measurement Unit
LQR = Linear Quadratic Regulator LTI = Linear Time Invariant
PSAS = Portland State Aerospace Society PWM = Pulse Width Modulation
RCS = Reaction Control System
I. Introduction
The Portland State Aerospace Society (PSAS) is an engineering student group and citizen science project at Portland State University dedicated to building low-cost, open-source, and open-hardware high-powered rockets and avionics systems. The group’s stated long term goal is to place a 1 kg cubesat into low Earth orbit with their own launch vehicle. This goal is set amidst the incredibly rapid expansion of the small satellite industry in this decade. Between 2013 and 2014 launches of nanosatellites, defined as satellites in the 1-10 kg mass range, increased by 270% according to SpaceWorks Small Satellite 2014 annual market analysis. Presently the small satellite market is handicapped by the limited selection of dedicated launch services options; satellite operators must choose between launch rideshares as a secondary payload (either on commercial launches or through NASAs Cubesat Launch Initiative) or deployment from the ISS Nanoracks system. In either case the satellite operator must cede ultimate control over the satellite orbital parameters to the launch services provider’s primary customer. Because this place a substantial limitation on the utility of small satellites a number of efforts are currently underway to develop dedicated launch vehicles to service the small satellites market, including a NASA request for proposals for “Venture Class Launch Services” capable of inserting up to 60 kg of U-class satellites (e.g. cubesats) into Low Earth Orbit. One fundamental technical requirement for these orbital rockets is a system for guiding the rocket along an orbital insertion trajectory; such systems are known as attitude control systems.
Downloaded by NASA GODDARD SPACE FLIGHT CENTER on September 21, 2015 | http://arc.aiaa.org | DOI: 10.2514/6.2015-4623

AIAA SPACE 2015 Conference and Exposition

31 Aug-2 Sep 2015, Pasadena, California

AIAA 2015-4623

Copyright © 2015 by Portland State Aerospace Society. Published by the American Institute of Aeronautics and Astronautics, Inc., with permission.

SPACE Conferences &amp; Exposition

Dedicated small satellite launch vehicles share cladistic similarities, at the extrema of their range, with both large orbital launch vehicles and the comparatively small high-powered rockets that have been operated by hundreds of amateur and university groups such as PSAS, for decades. Typically high-powered rockets fly ballistic trajectories with apogees nearly always less than 30 km and more commonly less than 10 km altitude. However, several of these amateur and university groups harbor aspirations of sub-orbital flight above the von Karman line. In the context of amateur and university high-powered rocketry groups, attitude control systems have many near-term potential applications and usage cases:
1. active stabilization,
2. trajectory control, dispersion envelope control and range safety,
3. science, payload, and instrumentation requirements,
4. atmospheric reentry energy management,

One direct application of an attitude control system in high powered rocketry is counteracting the deleterious effects of weather cocking (that is, the tendency of rockets to steer into the wind). Aerodynamic fins are often used in conjunction with nose cone weights to ensure the rocket’s center of pressure is well behind the center of mass such that corrective moments are produced for non-zero angles of attack. Weather cocking is a side effect of this need to use large fins for passive stabilization. Local wind speeds change the fluid velocity vector so that it is no longer strictly vertical for a rocket in flight. Ultimately this causes rockets to squander impulse in accelerating laterally. By using an attitude control system for active stabilization fin sizes can be reduced and the high-powered rockets maximum altitude at apogee can be improved.
Relatedly, very high altitude launches are constrained by range safety issues. Generally obtaining a FAA waiver for a Class 3 ‘Advanced High-Powered Rocket’ launch is contingent on being able to rigorously justify that the rocket will return to the Earth within some radius of the launch site that is safely distant from populated areas. This area within which the rocket must land is called the dispersion envelope. Unfortunately, ensuring an acceptably small dispersion radius becomes more and more difficult with increasing altitude at apogee, both due to weather cocking and the tendency of high altitude winds to translate the launch vehicle downrange. This introduces a novel usage case for an attitude control system. Using a combination of publically available NOAA data on high altitude winds and Monte Carlo simulation an initial heading and launch angle can be determined that will cause the rocket to land very near the launch site with a known level of statistical confidence. Using this information the boost guidance on the launch vehicle would, upon clearing the tower, immediately roll to align one of the pitch axes with the desired heading and then pitch over to the initial launch angle. This is known colloquially as “calling the shot”, and would be unprecedented as an in-situ capability for a launch vehicle in the high powered rocketry class. Presently such capability is attained by gimballing the entire launch tower rail.¹
In addition to boost guidance, rocket
attitude control enables support for
sensors or instrumentation with specific
angle or rate pointing requirements. For large suborbital sounding rockets a significant portion of the flight time is spent above the atmosphere (often as long as five minutes). At this altitude, free-fall
conditions | prevail | and | perturbing
aerodynamic torques are small such that an attitude control system can provide a stable actively pointed platform for experimentation with minimal disruption from controller vibrations. Research areas that benefit from such technology
include | microgravity | fluid | physics,
meteorology and atmospheric science, infrared and x-ray astronomy. Should an
inexpensive, | open-hardware | attitude
control system be developed that is scaled for university class sounding rockets, then some of these rockets may
eventually | be | evolved | into | more

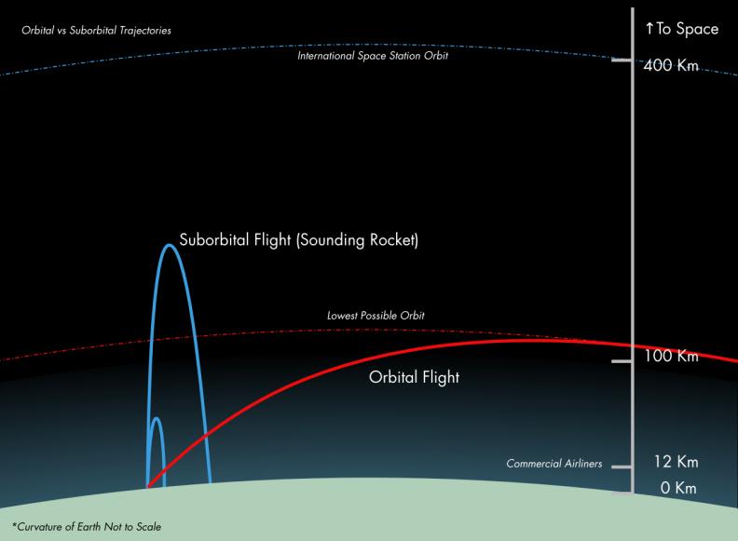
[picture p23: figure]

Figure 1. Comparative schematic of orbital and suborbital trajectories (image courtesy of PSAS).

Downloaded by NASA GODDARD SPACE FLIGHT CENTER on September 21, 2015 | http://arc.aiaa.org | DOI: 10.2514/6.2015-4623

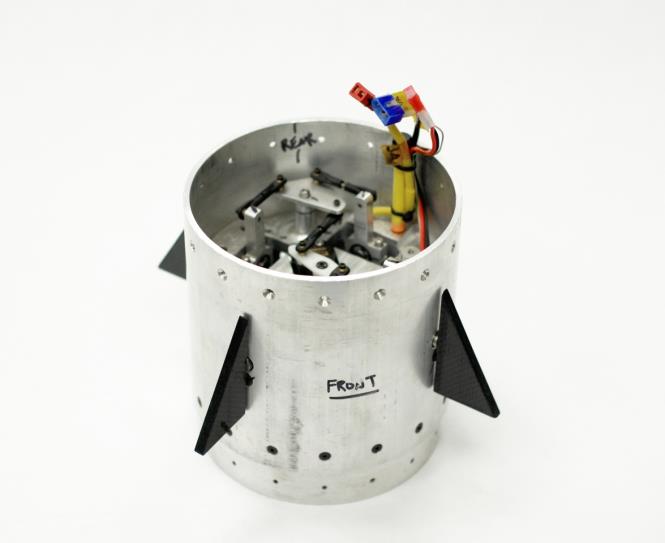
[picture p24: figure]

generally capable platforms for research in these fields. Other payloads and subsystems can benefit from directional pointing as well, such as cameras and telemetry downlink antennas.
Another application is energy management during payload reentry. During the atmospheric reentry phase of a suborbital trajectory enormous heat and dynamic pressure loadings develop as the launch vehicle decelerates from several kilometers per second ground relative velocity. Mitigating the
effect | of | these | loadings | is | critical | for
comparatively small scale single-stage launch vehicles that are intended to be recovered and reused, such as many university group operated high powered rockets. An attitude control system can be used to place an initial spin on the launch vehicle; as it reenters the atmosphere aerodynamic drag induces small torques on the spinning vehicle. Because of rotational energy dissipation, these small torques cause the spin to precess or nutate to the axis with the highest moment of inertia, in this
case | the | pitch/yaw | axes. | This | flat-spin
aerodynamic mode has the effect of increasing drag coefficients for the launch vehicle. The resulting increase in drag can be harnessed to bleed off excess velocity of the vehicle during reentry at an acceptably low dynamic pressure.
A yet more ambitious application of boost guidance and attitude control is trajectory optimization for orbital launches. Ascent trajectories for orbital launch vehicles differ in several key respects from sounding trajectories which otherwise do not require inertial guidance; these are schematically illustrated in Figure 1. Optimal ascent trajectories are designed to minimize overall launch delta-v requirements, however this is difficult because the relative magnitude of various losses, such as drag, gravity and steering losses are path dependent. Active control thus becomes a powerful tool for optimizing orbital launch trajectories.
Inside Earth’s atmosphere the most often used attitude control strategy is to actuate steerable aerodynamic control surfaces, such as fins or canards. Unfortunately, such systems are constrained by the dynamic pressure at which they can produce useful amounts of lift. Generally, this corresponds to a limiting flight envelope of about 30 km altitude.

Figure 2. LV2.3 Roll Control System (image courtesy of PSAS).


Figure 3. Portland State Aerospace Society LV2.3 and LV3 high powered rockets (images courtesy of PSAS).

Downloaded by NASA GODDARD SPACE FLIGHT CENTER on September 21, 2015 | http://arc.aiaa.org | DOI: 10.2514/6.2015-4623

PSASs current generation sounding rocket, LV2.3, is capable of a 5 km apogee and low supersonic velocities. It uses a module with servo-actuated steerable canards for roll axis attitude control, shown in Figure 2. In 2014 PSAS began work on a new very high-altitude high powered rocket, the LV3, with a design apogee of over 40 km. These vehicles are pictured in Figure 3. Pursuant to their mission of developing inexpensive, open-source technologies for small-scale orbital launch vehicles PSAS issued a call for a 6 degree of freedom attitude control system which could operate at these very high altitudes. This became the basis of a mechanical engineering senior capstone project at Portland State University.

II. Top-Level Design
A. Requirements
The essential design requirement for the attitude control system is that it must control the launch vehicle pitch, yaw and roll angles and velocities at all conceivable altitudes and in vacuum conditions, with particular emphasis placed on the roll axis. The system should have at least 150 N•s of stored impulse. The system should use inexpensive COTS components. The system should also be expressly designed with extensibility and scalability in mind. This requirement follows from PSASs general
interest in open-source development of
technologies for high powered rocketry, and the
fact that LV3 is presently in the preliminary design phase and its mass characteristics and trajectory design are still subject to change.
B. Baseline Design
The baseline attitude control system design is a cold-gas vernier jet type Reaction Control System (RCS) as seen in Figure 4. The RCS module is designed to fit ⌀6.o” payloads. The RCS module itself is physically composed of a high-pressure nitrogen propellant tank, a regulator, a series of 6 solenoid valves (two for roll, and four for pitch/yaw) plumbed to 8 3D printed rocket nozzles, a power supply and MOSFET relay board, an Intel Edison microcontroller with an Arduino breakout board, an inertial measurement unit, a set of pressure transducers, miscellaneous plumbing (gas lines, push to connect fittings, compression fittings, a fill valve, a latch valve, a high pressure tank adaptor, a gas distributor manifold, burst disks, etc.) a structural frame, and a carbon-composite aeroshell. The set of 8 vernier jet rocket nozzles are arranged such that they are perpendicular to the 3 principle axes of rotation of the rocket. When the solenoids are energized nitrogen gas exhausts supersonically through the rocket nozzles producing thrust. These thrust forces act across a lever arm to the vehicle center of mass to produce moments of force which then steer or orient the vehicle in whatever direction is desired. Cold-gas propulsion systems, while of generally low performance, are inexpensive, mechanically simple, and safe to operate such that they can be used by high turnover university student groups. The open-source/open-hardware and scalability requirements for different missions led to the selection of a modular system layout


Figure 4. RCS Piping and Instrumentation Diagram, RCS roll test module in acrylic display case, and Solidworks® render of RCS assembly.

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

with 3D printed nozzles, and a controller robust enough to tolerate large variances in system dynamics and model uncertainty, and that is relatively straightforward to determine gains via simulation.

III. Propulsion
Nitrogen cold-gas has comparatively low theoretical specific impulse of about 70 s at 100 psi chamber pressure and standard temperature. This means that the ratio of mass flow rate to developed thrust is high and thus is inefficient. Since there are both volume and mass constraints on the total amount of propellant that can be carried on the rocket some analysis was required to optimize nozzle performance where possible. Additionally for a scalable, open-source system a way is required to ensure that the numbers that are put into the plant model in the controller are accurate. An essential property of rocket nozzles is that their design expansion ratio is optimum for only a single ratio of back pressure to chamber pressure. This optimal performance therefore corresponds to a single specific altitude of operation. Problematically, for any sub-orbital sounding trajectory the altitude, and thus the back pressure, changes rapidly with time. One primitive, but analytically straightforward approach to determining the back pressure is simply to use an averaged ‘characteristic altitude’ value associated with a mission design flight envelope in combination with the US 1976 standard atmosphere model. Using additive manufacturing techniques we gain the flexibility to rapidly manufacture optimal nozzles on the fly to fit any specified mission trajectory, or launch vehicle mass characteristics by varying nozzle throat area, and
expansion ratio parameters.
An ideal nozzle is shaped such
that all flow is axial at the exit plane, eliminating divergence
losses, | however | such | ideal
nozzles are infinitely long and so cannot be used for practical propulsion. Since 1960 Rao’s
method | of | characteristics
approach has been used to
analytically | determine | the
contour | needed | to | achieve
optimal (i.e. uniform parallel) flow conditions at the exit plane.² This requires that flow be inviscid and 2-D, however since real flow is viscous a boundary layer correction must be applied ex post facto. For large rocket nozzles these losses are comparatively small (generally less than 1.0 %).


3
Nozzles with throat Reynolds numbers greater than 10⁶
are not
believed to have significant boundary layer losses.⁴,5 For small nozzles there is potentially a much larger effect.
The Rao perfect nozzle is not a parabola, however it resembles
one and can be reasonably be
approximated | as | one. | Such


nozzles are commonly termed ‘Bell nozzles’. These nozzles can be shorter than conical nozzles of equivalent expansion ratio. The significant divergence losses in conical nozzles can only be reduced by reducing the divergence angle. For the same expansion ratio this means that the nozzle will have to be longer. As the 3D printed nozzles are real rather than ideal nozzles, added length has the effect of increasing boundary layer and frictional losses, which are compounded by the combination of small throat area, rough interior surface finish and low chamber pressure. A further advantage of additive manufacturing in that it enables use of the Rao bell paraboloid nozzle which are normally difficult to manufacture at very small scales using conventional machining techniques.

Figure 5. Roll axis scarfed geometry nozzles SolidWorks® CAD drawing.

Figure 6. 3D Printed nozzle SolidWorks® CAD drawing and single-stream test nozzle.

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

A simple procedure was developed which makes this approach very easy to scale. First, the known back pressure and desired thrust are used as arguments in a simple MATLAB® script to determine throat area and optimal expansion ratios for the RCS nozzles. Initial and final angles, and convergence radii of the ideal Rao paraboloid approximation are determined from a lookup table using the expansion ratio and percent bell.³ These values are input into a SolidWorks® parametric model of the rocket nozzles. As the RCS module is inline, nozzles were scarfed, as seen in Figure 5, to conform to the airframe outer diameter. This unfortunately incurs a small cosine loss as the thrust vector is no longer coplanar with the nozzle axis of radial symmetry. Effective expansion ratios for the scarfing were determined using a straightforward root mean square approach.⁶ Lastly SolidWorks® is used to export “.stl” files that can be sent to any commercial 3D fabricator for printing. The RCS nozzles were printed on a 3D Systems ProJet® 3500 HD Max printer. The production media, VisiJet Crystal, is relatively durable, and can be tapped for threaded inserts or fittings. An example of a 3D printed test nozzle can be seen in Figure 6.
The first major step in the nozzle design process was determining the thrust level required of the system. Starting with the equation of motion

Iθ̈= T
(1)

where I is the mass moment of inertia, θ̈is the angular acceleration, and T is the torque. Furthermore, torque is defined by the equation,

Fr = T
(2)

where F is thrust force and r is lever arm (i.e. launch vehicle outer radius). Substituting (2) into (1) leads to the equation for the required thrust force (uncoupled)

F =

Iθ̈
r

It was desired for LV3 to be able to conduct snap rolls off of the tower to support the “call the shot” usage case. This called for a maximum case 45˚ roll program to be completed in 1 s, requiring 0.80 rad/s² of angular acceleration. Given this value, and the worst case expected values of mass moment of inertia and lever arm of LV3 in roll, the thrust required from the roll nozzles is only 6.0 N.


Figure 7. LV2.3 Roll force telemetry used for estimating baseline for RCS performance.


Figure 8. Simulation output used for flow componentry selection.

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

Another design consideration is an estimate the required delta-v for maneuvering and active attitude stabilization, which is important for trade off analysis of rocket fin size as well as propellant tank size. Unfortunately there does not seem to be a straightforward analytical approach to determining impulse budgets for launch vehicle attitude control. Therefore the impulse budget, along with the magnitude of dynamical perturbations affecting the airframe generally, was estimated using launch telemetry from PSASs LV2.3. It was determined that the average perturbing force acting on LV2.3 was 1.49 N. Integrated over a 30 second period of active control this translates to required impulse budget of 45 N•s to maintain roll rates at 0 rad/s²
, neglecting any additional planned maneuvers. Given an initial tank pressure of 3500 psi and isothermal emptying conditions this translates to a required tank volume of 0.885 L. A roll force plot constructed from LV2.3 telemetry is presented in Figure 7. It is desirable that the ratio T/I be large enough to zero out initial rates to the satisfaction of any response time requirements, and to exceed the magnitude of any expected disturbing torques by a large margin, but yet no so large that attitude hold fuel-efficiency is negatively affected with a sub-nominally damped control response. Based on the assumption that the disturbing torques are similar between LV2.3 and LV3 a design thrust of 8.0 N was chosen for the RCS roll nozzles. The propellant tank is a Luxfer composite 2 L cylinder with a specified service pressure of 4500 psi. Given a design pressure of 3500 psi the tank should have a mission impulse budget factor of safety of close to 2.
Additional simulations of tank and nozzle thermodynamics were used to determine required flow coefficients for the various flow components in the system, particularly of the solenoid valves and the pressure regulator. The model used discrete time iteration to model the changing tank conditions using the Van der Wall equations of state and the isentropic relations, in addition to the non-choked flow coefficient equations. This was done to ensure that choked flow conditions would hold only at the nozzle throat and thus that the nozzle would operate supersonically. This helped inform the COTS component selection of the detailed design phase of the engineering process. An example model output plot for the case of a flight-like nozzle with a 100 psi chamber pressure nozzle operated at sea level with an expansion ratio of 2, inlet temperature of 290 K, initial tank pressure of 3500 psi, and a throat area of 1.26x10⁻⁵ m² is
shown in Figure 8. These simulations indicated that for the isentropic tank emptying condition at the expected duty cycles, and initial conditions propellant temperatures would rapidly drop to the region 70-90 K. This is close to the saturation temperature of nitrogen at 1 atmosphere. Though it was understood that the tank would not empty in a purely isentropic mode, a naively applied lumped capacitance analysis of the thermal response of the solenoid valves was conducted. This analysis conservatively assumed that only the solenoid armature absorbs heat, and made use of the Dittus-Boelter Nusselt number correlation (i.e. assuming that the flow is turbulent and fully developed though the solenoid). It was determined from this analysis that Biot numbers were large and that the characteristic time was of the same order of magnitude as the solenoid open time. This led to the selection of solenoid valves with Buna-N seals, which are expected to maintain integrity against leaks at temperatures as low as -40 C.

IV. Controller
A. Modeling
For the rotational tests, a simple proportional controller was used. This controller satisfied the key requirements without adding unnecessary complexity to the overall system. The creation of the RCS roll controller is broken into two methods: the theoretical modeling of individual blocks formed into a working system, and the physical implementation of the model applied to the dynamic mechanical system. The model consists of 5 major blocks, the DC limiter, controller, PWM generator, solenoid model, and the rotational system transfer function (e.g. the rigid-body dynamics of the airframe). The system model is shown in Figure 9.


Figure 9. Simulink® block diagram of the rocket in roll.

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

A simplified transfer function, dubbed the flying cylinder, was created using system dynamics equations with respect to roll rate and disturbance force. Starting with the equation of motion and solving for the transfer function with the input as angular velocity and the output as force we obtain

θ̇
F

=

r
Is + b

where θ̇ is the rotational velocity, F is the force, r is the radial position of the nozzles, I is the mass moment of inertia about the rotational axis, b is the damping ratio of air, and s is the Laplace frequency domain variable.
The On/Off solenoid valve block, used as the actuator, is modeled with the equation

1
τs + 1


where τ is the solenoid time constant; this model was used to simulate the discrete time lag of the solenoid. The time constant was determined through the manufacturer’s lag time claims and verified by single-stream testing the system. A PWM block was also included to simulate the force out of the solenoid as it is cycled. This then had to be normalized from a 0 to 1 range (PWM duty-cycle). A PWM frequency of 5 Hz was selected by optimization between the fastest response time and widest duty-cycle range. A duty-cycle of 10% was determined to be the fastest rate at which the solenoid could be reasonably pulsed at 5 Hz, to achieve low-end force control (i.e. to minimize the size of the smallest impulse bit).
The DC limiter constrained the
control duty-cycle to a workable range,
from 10% to 80% pulse width. This block transforms the required thrust force into solenoid duty cycle by use of a linear regression determined through PWM single-stream testing of the propulsion system. The range of the workable low-end duty-cycle was determined through thrust force data
collected | during | single-steam
propulsion testing using a load cell, and through qualitative analysis of the transient developing flow during PWM solenoid operation using Schlieren interferometry, as seen in Figure 10.
This | single-stream | analysis | also
included characterization of the open and close lags, time constant, and controllability of the duty-cycles for the
solenoid. | The | maximum | thrust
developed by the nozzles was also
determined | through | single-stream
testing and compared to predictions from isentropic theory. The single-stream test apparatus is shown in Figure 11.


Figure 11. Single-stream test apparatus.

Figure 10. Single-stream testing Schlieren interferometry.

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

B. Implementation and Results
To help parallelize development, an open loop controller was initially used to qualitatively test the assembled system for operational performance, specifically scalable control forces, and equal forces from opposing nozzles. Additionally an LED simulator with full feedback control was rapily prototyped to qualitatively analyze the control law, sensor characteristics, and electronic system response. This proved useful quickly buying down development risk, identifying bugs, and avoiding unnecessary pressurization of the full roll-control RCS in advance of a test, which could be a time-consuming exercise. The feedback controlled simulator used an Arduino Uno microcontroller and a 6-DoF IMU (MPU-6050) for the on-board sensor. The 6-DoF LED simulator is shown in Figure 12. For the full roll-control RCS system an Intel Edison microcontroller was used in lieu of the Arduino Uno. Running the Ubilinux operating system, a Debian distribution targeted for use in embedded device applications, the RCS controller leveraged the Edison’s substantially improved performance and its wireless functionality. During captive wire-suspended tests a moment was applied to the rocket body, and the controller would then decrease the roll rate to zero. The data collected from the roll tests was then compared against simulation outputs. The roll rate accuracy was determined to be ±2 deg/s. The expected critical damping and settling time of under 80 ms from the model aligned well with the experimental test results as seen in Figure 13. The model is validated further by comparing model and experimental disturbance rejection as seen in Figure 14, simulating real world forces that are counteracted by the RCS. Using Bode analysis in MATLAB® we estimate that the controller has over -6 dB of gain and 60° of phase margin. This satisfies the robust control requirement, as the controller will tolerate dynamical changes in the plant and/or model uncertainty of over %50.

7


V. Ongoing and Future Work The RCS controller satisfies the baseline requirements outlined in the original project scope, however further development is necessary to enable robust 6-DoF control. Validating the roll model allows us to project the control logic to the pitch and yaw angles. A rigid-body 6-DoF dynamical model of the entire launch vehicle, shown in Figure 15, was developed in Simulink to provide a medium to simulate the rocket’s flight path and controller dynamics. This model contains multiple models that function as independent systems of the rocket throughout varying flight regimes; it serves as a stepping stone moving forward with the development of a fully controlled six degree of freedom RCS.

Figure 12. LED 6-DoF simulator.

Figure 13. Impulse response of the RCS in roll. The simulation data is plotted against the collected experimental data.

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


Following from the extensibility and scalability requirement is the planned implimentation of a Linear Quadratic Regulator (LQR) controller. This controller implementation is attractive due to their intrinsic robustness and ease of determining gains which are important advantages for a system that cannot be feasibly tested in physically realistic conditions prior to first flight. The ease of determining gains should also smooth the process of adapting the controller for use on other sounding rockets. Further capabilities enabled by LQR include gain scheduling via Linear Time Invariant (LTI) techniques, which has the potential to further improve the controller robustness as the fundamental dynamics of rocket flight change in different aerodynamic (subsonic, transonic transition, supersonic) regimes. While the rocket is not a Linear Time Invariant system, it can be modeled as one by scheduling optimized gains at different altitude ranges offering the more control authority over continuously changing flight conditions. Gain scheduling helps make the control logic tolerant of the time varying dynamics of the system plant. LQR also allows the use of cost minimization functions which provides an
elegant approach to preventing waste of the finite
supply of consumable propellant.⁸
To increase controllability of the system, state-space equations for rigid body attitude dynamics will be implemented; these can be found in some advanced aerospace controls texts.

9 They account for the damping on the rocket in different aerodynamic regimes. These can still be used effectively with the LQR controller. The controller can also be assigned a hierarchy of desired control states with varying weight. The controlled states consist of rotational position and velocity, translational position, and quaternions. Quaternion representations are useful in that they help avoid gimbal locking and account for dynamic cross coupling between different control axes. Further research is planned to model this behavior and implement it in the 6-DoF flight controller.


VI. Conclusion
As it stands the LV3 RCS is one of the only operational high powered rocketry class cold-gas attitude control systems in the world, and is also to the best knowledge of authors, the first such system designed entirely by a team of undergraduate students. The RCS module will be integrated on the PSAS LV3 stack for a demonstration flight in spring of 2016. Test risks associated with active control in the pitch/yaw axes will be mitigated by using the RCS in a roll control capacity only for its inaugural flight, however the system will be capable of full attitude control. Ultimately, there is very little inherently new in designing cold gas attitude control systems; such systems already have a very high technology readiness level. Currently attitude control systems are not widely used by university rocketry groups largely for cost and technical complexity reasons. However, in view of its many applications, RCS remains a key enabling technology for the burgeoning field of high powered rocketry and ultimately, low cost space access as well.

Figure 14. Disturbance rejection of the RCS in roll. A constant torque was applied to the RCS, inducing a constant disturbance. The controller was set to keep the angular velocity at zero. As shown in the disturbance rejection of error graph, the simulation closely models what is happening in the real world.

Figure 15. Simulink® model of a 6 DoF rigid-body rocket.

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

Acknowledgements
The authors are indebted to Dr. Ross Gadient and to the PSAS Advisors Andrew Greenberg, and Nathan Bergey for their support and advice. They are further indebted to Faculty Advisor Dr. Mark Weislogel for his advice and financial support. To ECE post-baccalaureates Aaron Baker and Kyle Lu for electrical engineering support. To PSUs Dryden Drop Tower Lab, and the Lab for Interconnected Devices for logistical support. To the PSU Beta Project for financial support as well as to the 60 PSAS crowdfunding campaign backers who raised over $10,000 to help fund the RCS capstone as well as four other 2015 PSU MCECS capstones. To Corwin Whitefield and 3D Fixtures Inc. for extremely generous 3D printing in-kind donations. To Advanced Flight Systems Inc. and the PSU ME Machine Shop for donated machine time and tooling. To instructibles.com and Intel for the donation of an Intel Edison development board.

Reference

1
Jung, W., Gomes, R. M., Louis, J. E., Neto, O. S., “Aeolus- Wind Weighting Program and Concept for Unguided Suborbital Launch Vehicles,” 19th ESA Symposium on European Rocket and Baloon Programmes and Related Research, ESA SP-671, 2009.
2Allman, J. G., and Hoffman, J. D., “Design of Maximum Thrust Nozzle Contours by Direct Optimization Methods,” AIAA Journal, Vol. 19, Jun. 1981, pp. 750–751. (https://www.researchgate.net/publication/253895719_Design_of_Maximum_Thrust_Nozzle_Contours_by_Direct_Optimization_Methods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)
3Sutton, G. P., Biblarz, O., Rocket Propulsion Elements, 7th Edition, New York: Wiley-Interscience, 2000, pp. 80, 87.
4 (https://www.researchgate.net/publication/243384988_Rocket_Propulsion_Elements?el=1_x_8)Massier, P. F., Back, L. H., Noel, M. B., and Saheli, F., “Viscous Effects on the Flow Coeffcient for
a Supersonic Nozzle," AIAA Journal, Vol. 8, No. 3, March 1970, pp. 605-607.
5 (https://www.researchgate.net/publication/4684974_Viscous_effects_on_the_flow_coefficient_for_a_supersonic_nozzle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)Brinich, P. F., Jack, J. R., and Spisz, E. W., “Thrust coefficients of low-thrust nozzles”, NASA TND-3056, 1965. 6 (https://www.researchgate.net/publication/4684974_Viscous_effects_on_the_flow_coefficient_for_a_supersonic_nozzle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)Obrien, C. J., “Unconventional nozzle tradeoff study”, NASA CR-159520, 1979. (https://www.researchgate.net/publication/4684974_Viscous_effects_on_the_flow_coefficient_for_a_supersonic_nozzle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)

7
Jeb Orr, and Tannen Van Zwieten, “Robust, Practical Adaptive Control for Launch Vehicles,” AIAA Guidance, Navigation, and Control Conference, American Institute of Aeronautics and Astronautics, 2012.
8 (https://www.researchgate.net/publication/268557572_Robust_Practical_Adaptive_Control_for_Launch_Vehicles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)Martinez, C., “Digital attitude control for NASA sounding rockets,” Proc. SPIE 3442, Missions to the Sun II, 1998, pp. 157–165. (https://www.researchgate.net/publication/252973382_Digital_attitude_control_for_NASA_sounding_rockets?el=1_x_8)
9Wie, B., Space Vehicle Dynamics and Control, Reston, VA: AIAA, 2008. (https://www.researchgate.net/publication/267655641_Space_Vehicle_Dynamics_and_Control?el=1_x_8)
Downloaded by NASA GODDARD SPACE FLIGHT CENTER on September 21, 2015 | http://arc.aiaa.org | DOI: 10.2514/6.2015-4623

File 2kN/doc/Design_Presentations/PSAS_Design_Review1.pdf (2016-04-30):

# Liquid Fuel Rocket Engine

## Portland State Aerospace Society Senior Capstone Project

Tamara Dib, Taylor Rice, Kristin Travis,

## John Tucker, Bianca Viggiano, Cam Yun

# Engine Design

-250 lb Thrust

-Static test stand engine

-3D printed in Inconel


-Ethanol and Liquid Oxygen Propellants

-Fuel filled regenerative cooling channels

-Fuel centered stainless steel pintle injector

# Engine Design


Ethanol
Inlet

Cooling
Channels

Ethanol Manifold

LOX
Manifold

Ethanol

Copper Crush
Gasket

Pintle Injector

1.24 in | 0.789 in | 2.5 in

5.17 in

# Pintle Design


Ethanol Holes (20 total) = 0.01” x 0.03” | 0.28”
LOX annulus gap = 0.008”

0.03”

0.1”

# Injector

-Chamber pressure = 350 psi

-Mixture ratio = 1.25

-1.06 lb/s total flowrate

-0.48 lb/s ethanol

-0.58 lb/s lox

-Pressure drop across injector = 70 psi

-Blockage Factor = 0.76

-Total Momentum Ratio = 0.83

-Effective Momentum Ratio = 1.08

# Cooling Channels


Cooling Channel Section at Nozzle Throat | Cooling Channel Section at Combustion Chamber

-Cooling channels maintain a constant cross sectional area

Outer Wall Thickness
= 0.012”

Inner Wall Thickness
and Lands = 0.006”

# Heat Transfer and Stress Analysis

-Pr = 0.88

-Required q at the throat = 33.84 Btu/in^2-s

-Wall thickness = 0.00615 in

-Combined tangential stress at nozzle exit = 669.52 psi

-Combined tangential stress at throat = 130473.88 psi

-Max compressive stress at coaxial shell design = 49117.22 psi

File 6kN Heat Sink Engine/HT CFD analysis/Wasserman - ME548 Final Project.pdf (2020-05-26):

# Modeling of a Liquid-Propellant Heat-Sink Rocket Engine

ME448/548: Final Project
Marc Wasserman
March 20, 2020

## Introduction

The Portland State Aerospace Society (PSAS) is developing an alcohol-liquid oxygen rocket engine to power its next generation LV-4 rocket. PSAS previously attempted to build a fully-functional, small scale prototype but encountered difficulties with the cooling channels, rendering the entire 3d engine inoperable. To allow for testing of the thrust and combustion chamber with minimal added complexity, PSAS is now developing a heat-sink engine without any active cooling. This type of engine is generally understood to only be suitable for firings of a few seconds [1], however this should be enough to validate the design.

Because the engine combustion temperature is expected to be about 3100K, one of the key challenges of designing a heat-sink engine is determining how long it can be fired before the engine wall melts. PSAS is currently weighing whether to use a cheaper Aluminum or a more expensive stainless steel for the engine. The goal of this project is to create a CFD simulation using Star CCM+ that models the proposed engine design and determines how the choice of material will affect the amount of time the engine can be fired before melting occurs.

## Physical Model and Boundary Conditions

### Rocket Parameters

At its most basic, a rocket engine is an application of the classic converging-diverging nozzle which compresses subsonic flow through a constriction, creates choked flow at the narrowest point and allows for supersonic expansion through the bell. The important parameters of a rocket engine are its thrust, chamber pressure, stagnation temperature, mass flow rate, throat area and exit area. These values, shown below in Table 1, have been determined by other work at PSAS and have been used to create the rocket profile used for this simulation.

Table 1: Rocket parameters for the test engine. Most values provided by PSAS design optimization work [2].

Parameter | Metric | US
Desired thrust | 6 kN | 1350 lbf
Mass flow rate | 2.62 kg/s | 5.76 lb/s
Chamber pressure | 2.41 MPa | 350 psi
Chamber temperature | 3100 K | 5580 R
Chamber cross-section area | 9.13e-3 m² | 14.2 in²
Throat area | 1.83e-3 m² | 2.835 in²
Exit area | 8.35e-3 m² | 12.94 in²

The rocket engine used for this simulation is shown below in Figure 1. This engine has been designed by PSAS using the theoretical rocket equations described in Huzel & Huang and combustion parameters from CEARun, a combustion analysis program created by NASA.


Figure 1: PSAS heat sink rocket engine prototype cut section. Dimensions are in mm. The section used in the CFD model extends from the start of the straight section on the left to the end of the bell on the right.

### Key Equations & Assumptions

An important simplification for this simulation is that air is used in the model instead of actual combustion products. This is done because the properties of air are well established and its material properties are part of the standard Star CCM+ library. Because gases tend to act more like ideal gases at high temperatures, air is expected to be a reasonable analogue for the actual combustion products.

Some of the key equations used to determine the expected flow behavior and validate the simulation outputs include:

- Dynamic viscosity of air: μ = 1.46x10⁻⁶

[

T

3/2
T+111] Ns/m²
[4]
- Density of an ideal gas: ρ =

P
RT

[4]

- Reynolds number: Re =

ρVD
μ

[5]
- | Speed of sound in an ideal gas: c = √RTk | [4]
- Pressure ratio (isentropic flow): p
| ∗ = p0 [

2
| k+1

]

k/(k−1)
| | [4]
- Diffusion time scale: t
| ∗ = L
| 2 α

These equations are solved below in Table 2. The Reynolds number found is used to determine whether a turbulent or laminar model is most appropriate, the time scale guides the choice of time step, and the remaining values are used to compare the hand calculations to the simulation results.

Table 2: Fluid parameters for the CFD Model. For this model, air is used instead of the actual combustion products.

Parameter | Value
Temperature [2] | 3100K
Air density | 2.708 kg/m³
Gas constant for air [3] | 287 J/kgK
Chamber diameter | 0.1078 m
Throat diameter | 0.0483 m
Velocity through chamber | 9.13e-3 m²
Air dynamic viscosity, 3100K | 7.8e-5 Ns/m²
Reynolds number | 3.78e5
Speed of sound at throat | 1116 m/s
Throat pressure | 12.75 bar
Wall thickness | 0.004 m
α-Aluminum / α-Stainless [6] | 97.1e-6 / 13.4e-6 m² /s
Diffusion time scale, Al | 0.164 sec
Diffusion time scale, SS | 1.19 sec

## StarCCM+ Software Setup & Features

The actual part used in CFD simulation, shown below in Figure 2, was created in Solidworks using the geometry of the engine, however the leftmost portion containing the fuel injection manifold is removed to create a simpler surface to act as an inlet. The engine wall geometry is also modified by removing the structural honeycombing designed to support the bell. This change will affect the results by eliminating conduction through these fins, however it is expected that the engine will melt before fin cooling becomes important.


Figure 2: Part geometry used for StarCCM+ simulation. Dimension are identical to the model shown previously, with simplifications described in the text. The large, lower portion is the fluid region and the thin body on top is the solid region.

To simplify the model and reduce runtime, a 2D axisymmetric model is used to take advantage of the rotational symmetry of the part. With a flat model, the total number of cells is dramatically reduced compared to a 3D mesh with similar base size. This allows the model to run more quickly at a finer mesh size at the cost of less insight into three dimensional flow phenomena. Running on 4-cores in parallel, this simulation runs in approximately 10 minutes.

### Model Selection

Because rocket mechanics require compressible flow, the fluid region is configured with ideal-gas-compressible and coupled flow models. Because of the Reynolds number, turbulence is expected, and so the K-ε turbulence model has also been selected. The Star help documentation suggests that K-ε turbulence model offers a good compromise between computation intensity and robustness including in scenarios which model heat transfer [7]. The wall of the engine is modeled with coupled solid energy and a constant density as only heat transfer is being considered at this time. Both regions use an implicit unsteady model with expert initialization turned on to simulate the transient heating of the engine wall.

### Boundary Conditions

The two key boundary conditions in this simulation are the inlet and outlet conditions. The inlet of the engine, corresponding to the left surface in Figure 2, is modeled as a stagnation inlet with temperature and pressure from the engine parameters in Table 1. The outlet is configured as a pressure outlet with an ambient pressure of 1 bar. The interface between the two regions is set as a conjugate heat transfer boundary, and the initial wall temperature is set at 100K to reflect the system prechill with liquid Oxygen. All other conditions have been left at their default values.

## CFD Mesh Setup

The mesh used for the fluid region is a 2D polyhedral mesh with a base size of 0.4mm and 5 prism layers. The surface growth rate for the fluid mesh is reduced to 1.1 to create a denser mesh in the throat and bell areas. The fluid region contains a total of 19,190 cells. The solid region is meshed with quadrilateral elements at a base size of 0.4mm, approximately 10% of the wall thickness, resulting in a mesh of 4,602 cells. Both meshes pass internal mesh diagnostic report with no invalid cells.


Figure 3: Final mesh of the fluid and solid regions. Both regions are meshed with a 0.4mm base size for a total of ~23,800 cells.

To better illustrate the sizes of the solid and fluid mesh, Figure 4 shows a zoomed-in view of the throat region of the engine. The green line is the contact boundary between the solid and fluid regions.


Figure 4: zoomed in mesh view of the throat region showing relative sizes of fluid and solid region meshes.

## Results & Discussion

### Model Validation

Before considering the temperature results, the model is first inspected to see how closely it matches the rocket design reference materials, basic compressible flow equations, and ensure that conjugate heat transfer is working. The first, and most basic, requirement of a rocket engine is that it should create choked flow at the throat and supersonic exhaust, shown below in Figure 5, which plots the Mach number and pressure values along the central axis of the engine.


Figure 5: Mach number and pressure along the center axis. The zero-point is where the narrowest part of the engine occurs. The sonic transition at the axis is slightly downstream of the throat.

Seen in the plot above, when the red Mach number = 1, the green pressure line indicates a pressure of approximately 12.8 bar, which is close to the 12.75 bar calculated from the isentropic pressure ratio equation. Looking at the Mach number as a field in Figure 6 below, the actual shape of the sonic surface is that of a dome rather than flat as I originally anticipated. Upon further investigation, this shape matches the Mach assumptions described in Huzel and shown in figure 4.13 (located in the Appendix). The nonuniform exhaust velocities are also similar to those described by Huzel in the same section.


Figure 6: Mach number field through engine section. This field is from the Stainless Steel model run however the flow field is identical for both engine material types.

To confirm that conjugate heat transfer is working as expected, Figure 7 shows the temperature field through the fluid and solid regions of the stainless steel model. Huzel & Huang state in chapter 4 that the highest heat flux is experienced in the throat, and this behavior can be seen in the scalar scene below where the lightest wall colors occur just upstream of the throat. There is also a light spot at the very left edge of the wall, however this is likely an artifact of how the engine was truncated to simplify the inlet surface rather than a real phenomenon. In the real engine, the fuel injector will be located in the center of the engine, so the inlet hotspot seen below would not exist.


Figure 7: Temperature field of the 316SS model after 3.0s of elapsed time. The wall shows heating concentrated at the entrance and contraction region just upstream of the throat.

The temperature scene also shows the development of a boundary layer of cooler gas. The gas temperature is prescribed at the inlet on the left side, so the gas cools as it flows through the engine. This is expected, however it is also a potential source of model error. There will certainly be boundary layer formation in the actual engine, however with combustion occurring throughout the engine chamber, the boundary layer may differ from that formed in this model.

The final model validation test is a mass flow report. A good model will show only a small difference (ideally zero) between the mass flow in and out. As Figure 8 shows, the model has only a 2e-5 kg/s difference between the amount of air flowing in and flowing out, or a model error of about 0.004% of the flow rate.


Figure 8: Mass flow report showing the error in the model's continuity equation.

### Surface Temperature: Aluminum-walled Engine


Figure 9: Metal surface temperature for the Aluminum engine wall. The temperature probe points plotted in this graph are the dots shown in Figure 5, ordered in the legend as they appear in Figure 5 from left to right.

For 6061 Aluminum alloy, its liquidus temperature is 580°C [8]. The Contraction2 probe in Figure 9 reaches this wall temperature after approximately 1.25 seconds of simulated engine firing. The engine wall is even being modeled with an initial temperature of 100K to account for the engine prechill with liquid Oxygen, however the difference between an ambient and a chilled temperature start is less than 0.1 seconds before the melting temperature is reached. One surprising result of this run is that the wall in the middle of the combustion chamber heats much slower than the contraction region, only reaching 400°C by the end of the 2 second model run. The large discrepancy between the hottest and coldest temperature probes suggest that an overall surface average of the wall heat transfer would produce inaccurate results, and instead the focus should be on the specific regions that experience the highest heat flux.


Figure 10: Residuals plot for the Aluminum engine run. The smallest periodic oscillations of the residuals indicate the next time step. The reason for the longer periodic oscillations is unknown.

### Surface Temperature: Stainless Steel-walled Engine

Below in Figure 11 and Figure 12 are the model results for the stainless steel model run. The only differences between this model and the prior model run are the change of wall material and the extension of the physical time to 3.0s from 2.0s. Interestingly, the time to reach 500°C for the stainless steel engine is actually faster for the stainless steel model at 0.9s compared to the Aluminum’s 1.0s. The primary difference between the two models is that the melting point of 316 Stainless Steel is approximately 1400°C, so there is significantly a greater buffer before the surface melts.


Figure 11: Surface temperature graph for the stainless steel rocket wall. Temperature probes are unchanged from those for the Aluminum walled rocket.

As can be seen, even with the run time extended to 3 seconds, the highest temperature experienced by the stainless steel wall at the Contraction2 probe is 900°C, which is still 500°C below the melting point of the metal. This should allow enough buffer that the engine could be fired for several seconds without melting.


Figure 12: Residuals for the stainless steel rocket. The smallest scale oscillations are due to the inner iterations at each time step. The cause of the larger oscillations is unknown.

## Conclusion

Based on the two model runs shown above, stainless steel is superior to Aluminum for a heat sink rocket engine. While Aluminum has a thermal conductivity 17 times higher than 316 stainless steel [6], this increased conductivity is clearly overwhelmed by the convective heat transfer from the gas to the wall, illustrated by both metals sharing a similar heating curve. The stainless steel actually initially heats slightly faster than the Aluminum, which may be due to the lower specific heat of steel compared with Aluminum. Regardless, the advantage of stainless steel, at least for a heat sink engine, is its melting point of 1400°C. This heat tolerance allows the temperature of the wall to rise much closer to the temperature of the gas boundary layer, reducing the ΔT between the wall and fluid and slowing heat transfer. PSAS would like to conduct a test fire of approximately 3 seconds, and based on the results of this study, only a stainless steel design can be expected to survive.

Given additional time and resources, three areas where I would look to improve the model are the inlet conditions, the wall boundary layers and active cooling. While the stagnation inlet condition with hot air does produce a sonic transition and supersonic exhaust flow, Figure 8 predicts a flow rate of 0.58 kg/s. In contrast, the rocket equations in Huzel and the PSAS optimization scripts predicts a combined fuel/oxidizer mass flowrate of 2.6 kg/s, over four times great. I did rerun the model once with a mass flowrate inlet condition at the PSAS prescribed value and this produced a chamber pressure of 120 bar, well above the engine design pressure. It’s not clear why the CFD model predicts a mass flow rate so much lower than the theoretical rocket equations, however this discrepancy merits further investigation.

The second are I would improve with more time is the boundary layer behavior of the rocket. As mentioned earlier, the current model prescribes a temperature at the inlet, but then allows the temperature of the fluid to fall as it travels through the engine. This forms a cooler boundary layer as the gas progresses down the chamber wall. In a combustion process, the temperature of the inside of the engine chamber will be determined by the heat and mass balance of the system as it burns, so this may produce different boundary layer behavior than currently modeled. Additionally, the fuel injection system will be spraying liquid droplets into the engine, so in the fraction of a second before ignition, a fluid film would likely form on the inner surface of the engine which could act as an insulator as it boils off.

Finally, the design specification of LV-4 will require an engine burn time of approximately 30-45 seconds. Clearly neither an Aluminum nor stainless steel engine will survive a burn of that duration if it is uncooled. The addition of active cooling modeling would be a very useful extension of this simulation. This addition would likely require the conversion from axisymmetric to fully three-dimensional modeling to allow for investigation of different cooling channel geometries. If completed, however, a conjugate heat transfer model with active cooling would allow for virtual testing of engine designs before prototyping. Because PSAS is typically a budget-limited organization, an effective CFD model would have the potential to reduce cost and increase the potential for success by allowing for testing and design iteration before prototyping.

## References

[1] D. Huzel and D. Huang, Modern Engineering for Design of Liquid-Propellant Rocket Engines, Washington: American Institute of Aeronautics and Astronautics, 1992.
[2] "Parametric LFE Generation and Analysis," 16 March 2020. [Online]. Available: https://github.com/psas/liquid-engine-analysis/tree/master/LFE%20Design.
[3] E. Rathakrishnan, Instrumentation, Measurements, and Experiments in Fluids, Boca Raton: CRC Press, 2007.
[4] B. Munson, T. Okiishi, W. Huebsch and A. Rothmayer, Fundamentals of Fluid Mechanics, 7th ed, Hoboken: John Wiley & Sons, 2013.
[5] "Universal and Individual Gas Constants," 2020. [Online]. Available: https://www.engineeringtoolbox.com/individual-universal-gas-constant-d_588.html.
[6] F. Incropera and D. Dewitt, Fundamentals of Heat and Mass Transfer, 7th ed, Hoboken: John Wiley & Sons, 2011.
[7] "Deciding on a RANS Turbulence Model," 16 March 2020. [Online].
[8] Aerospace Specification Metals, Inc., "6000 Series Aluminum Alloys," n.d.. [Online]. Available: http://asm.matweb.com/search/SpecificMaterial.asp?bassnum=MA6061T6.

## Appendix

The figure below is from Huzel & Huang chapter 4 in discussing the behavior of rocket engine bells. The line T-O in the figure is described as the assumed Mach line through the engine bell. This bowed surface closely matches the simulation results found in Figure 6.


Figure 13: from Huzel & Huang chapter 4, illustrating the bell contours.

When the stainless steel model time is extended, the simulation predicts melting will occur after approximately seven seconds, nearly 6 seconds longer than predicted melting for the Aluminum engine.


Figure 14: Stainless steel model with the stopping criterion extended to 7 seconds of physical time.


The following is an example of the outputs from CEARun, used in designing the prototype engine:

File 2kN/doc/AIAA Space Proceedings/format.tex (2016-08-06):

% `template.tex', a bare-bones example employing the AIAA class.
%
% For a more advanced example that makes use of several third-party
% LaTeX packages, see `advanced_example.tex', but please read the
% Known Problems section of the users manual first.
%
% Typical processing for PostScript (PS) output:
%
%  latex template
%  latex template   (repeat as needed to resolve references)
%
%  xdvi template    (onscreen draft display)
%  dvips template   (postscript)
%  gv template.ps   (onscreen display)
%  lpr template.ps  (hardcopy)
%
% With the above, only Encapsulated PostScript (EPS) images can be used.
%
% Typical processing for Portable Document Format (PDF) output:
%
%  pdflatex template
%  pdflatex template      (repeat as needed to resolve references)
%
%  acroread template.pdf  (onscreen display)
%
% If you have EPS figures, you will need to use the epstopdf script
% to convert them to PDF because PDF is a limmited subset of EPS.
% pdflatex accepts a variety of other image formats such as JPG, TIF,
% PNG, and so forth -- check the documentation for your version.
%
% If you do *not* specify suffixes when using the graphicx package's
% \includegraphics command, latex and pdflatex will automatically select
% the appropriate figure format from those available.  This allows you
% to produce PS and PDF output from the same LaTeX source file.
%
% To generate a large format (e.g., 11"x17") PostScript copy for editing
% purposes, use
%
%  dvips -x 1467 -O -0.65in,0.85in -t tabloid template
%
% For further details and support, read the Users Manual, aiaa.pdf.

% Try to reduce the number of latex support calls from people who
% don't read the included documentation.
%
\typeout{}\typeout{If latex fails to find aiaa-tc, read the README file!}
%

\documentclass[]{aiaa-tc}% insert '[draft]' option to show overfull boxes

 \title{Bare-Bones \LaTeX\ Template for
        AIAA Technical Conference Papers}

 \author{
  First A. Author%
    \thanks{Job Title, Department, Address, and AIAA Member Grade.}
  \ and Second B. Author\thanksibid{1}\\
  {\normalsize\itshape
   Business or Academic Affiliation, City, Province, Zipcode, Country}\\
  \and
  Third C. Author%
   \thanks{Job Title, Department, Address, and AIAA Member Grade.}\\
  {\normalsize\itshape
  Business or Academic Affiliation, City, Province, Zipcode, Country}
 }

 % Data used by 'handcarry' option if invoked
 \AIAApapernumber{YEAR-NUMBER}
 \AIAAconference{Conference Name, Date, and Location}
 \AIAAcopyright{\AIAAcopyrightD{YEAR}}

 % Define commands to assure consistent treatment throughout document
 \newcommand{\eqnref}[1]{(\ref{#1})}
 \newcommand{\class}[1]{\texttt{#1}}
 \newcommand{\package}[1]{\texttt{#1}}
 \newcommand{\file}[1]{\texttt{#1}}
 \newcommand{\BibTeX}{\textsc{Bib}\TeX}

\begin{document}

\maketitle

\begin{abstract}
This is a bare-bones \LaTeX\ template of an AIAA technical conference paper.
It is intended to demonstrate the bare minimum set of \LaTeX\ commands
to produce an AIAA technical conference paper.
To explore more \LaTeX\ capabilities, see the advanced example, but
first read the Known Problems section of the user manual.
For detailed AIAA layout and style guidelines, please refer to the AIAA
author guide for paper submission, format, and other procedures.
\end{abstract}

\section*{Nomenclature}

\begin{tabbing}
  XXX \= \kill% this line sets tab stop
  $J$ \> Jacobian Matrix \\
  $f$ \> Residual value vector \\
  $x$ \> Variable value vector \\
  $F$ \> Force, N \\
  $m$ \> Mass, kg \\
  $\Delta x$ \> Variable displacement vector \\
  $\alpha$ \> Acceleration, m/s\textsuperscript{2} \\[5pt]
  \textit{Subscript}\\
  $i$ \> Variable number \\
 \end{tabbing}

\section{Introduction}

This would be a good place to insert some text that make sense relative
to the paper being written.
Of course, for example purposes, the text is quite meaningless.

\subsection{Background}

This background section is here only to demonstrate \verb|\subsection|
usage.
And following this, the next section level will need to be demonstrated.

\subsubsection{Detail}

Here is a \verb|\subsubsection| that would normally come in pairs of two
according to the requirements of an outline, but for the sake of
demonstration, we are only showing a single \verb|\subsubsection|.

\section{Model}

We should probably include some math.
Here we begin with Eq.~(\ref{e:function}) that demonstrates some math
typesetting.
\begin{equation}
 \label{e:function}
 \int_{0}^{r_{2}} F(r,\varphi) \, dr \, d\varphi =
    \left[ \sigma r_{2}/(2\mu_{0}) \right] \cdot
    \int_{0}^{\infty} \exp(-\rho|z_{j}-z_{i}|) \, \lambda^{-1} 
\end{equation}
Eq.~(\ref{e:function}) is grand.
Some say it is due to Rebek.\cite{rebek:82bk}

\section{Results}

In this section we will introduce some figures and tables.
It can be seen in figure~\ref{f:magnetic_field} that magnetization is a
function of applied field.
\begin{figure}[htb]% order of placement preference: here, top, bottom
 
 \caption{Magnetization as a function of applied field, which has
   borders so thick that they overwhelm the data and for some reason the
   ordinate label is rotated 90 degrees to make it difficult to
   read. This figure also demonstrates the dangers of using a bitmap
   as opposed to a vector image.}
 \label{f:magnetic_field}
\end{figure}
Sometimes writing meaningless text can be quiet easy, but other times
one is hard pressed to keep the words flowing.\footnote{And sometimes
things get carried away in endless detail.}
Meanwhile back in the other world, table~\ref{t:scheme_comparison} shows
a nifty comparison.
\begin{table}% no placement specified: defaults to here, top, bottom, page
 \begin{center}
  \caption{Variable and Fixed Coefficient Runge-Kutta Schemes as a
           Function of Reynolds Number}
  \label{t:scheme_comparison}
  \begin{tabular}{rrr}
       Re & Vary & Fixed \\\hline
        1 &  868 & 4,271 \\
       10 &  422 & 2,736 \\
       25 &  252 & 1,374 \\
       50 &  151 &   736 \\
      100 &  110 &   387 \\
      500 &   85 &   136 \\
    1,000 &   77 &   117 \\
    5,000 &   81 &    98 \\
   10,000 &   82 &    99
  \end{tabular}
 \end{center}
\end{table}

\section{Conclusion}

After much typing, the paper can now conclude.
Four rocks were next to the channel.
This caused a few standing waves during the rip that one could ride on
the way in or jump on the way out.

\section*{Appendix}

An appendix, if needed, should appear before the acknowledgments.
Use the 'starred' version of the \verb|\section| commands to avoid
section numbering.

\section*{Acknowledgments}

A place to recognize others.

\begin{thebibliography}{9}% maximum number of references (for label width)
 \bibitem{rebek:82bk}
 Rebek, A., {\it Fickle Rocks}, Fink Publishing, Chesapeake, 1982.
\end{thebibliography}

\end{document}

% - Release $Name:  $ -

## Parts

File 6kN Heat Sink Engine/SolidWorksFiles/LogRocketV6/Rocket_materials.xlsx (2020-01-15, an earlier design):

Combustion chamber and nozzle 2-part
Material - 1045 steel | Cost | Supplier | Note
Chamber - 6 in. dia. x 6 in. L - solid round | 136.52 | McMaster
Nozzle - 6 in. dia. x 9 in. L - solid round | 187.02 | McMaster
 | 323.54
DOM tubing chamber and 1045 nozzle
C1020 - Chamber - 6 in. OD x 1 in. wall x 6 in. L | 127.26 | SpeedyMetals
1045 - Nozzle - 6 in. dia. x 9 in. L - solid round | 187.02 | McMaster
 | 314.28
Material - 6061 Aluminum
Chamber - 6 in. dia. x 6 in. L - Tube - 1 in. wall (4 in. ID) | 125.19 | McMaster
Nozzle - 6 in. dia. x 12 in. L | 169.66 | McMaster | Can make both parts from 12" length if change L* to ~26 in
 | 294.85
Material - Gray cast iron tube and 1045/6061
Gray cast iron - Chamber - 6 in. dia. x 16 in. L - Tube - 1 in. wall (4 in. ID) | 232.97 | McMaster
Nozzle - 6 in. dia. x 9 in. L | 187.02
 | 419.99
 |  |  |  | * Shipping not included

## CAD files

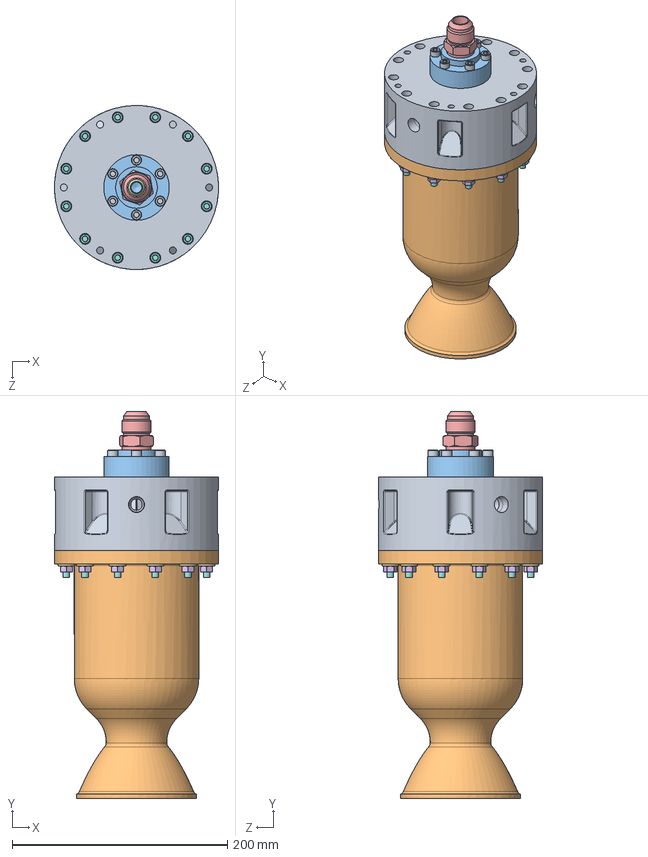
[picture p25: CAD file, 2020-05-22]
6kN Heat Sink Engine/SolidWorksFiles/hybridV2/HYBRID_MASTER.SLDASM
152.4 x 359.5 x 152.4 mm
injectorHead
chamber
pintleV7-5
5482K126_PRECISION AN 37 DEGREE FLARED TUBE FITTING
92673A116_ASTM F594 TYPE 18-8 STAINLESS STEEL HEX NUT x 12
91950A029_TYPE 316 STAINLESS STEEL SAE FLAT WASHER x 12
92196A329_18-8 STAINLESS STEEL SOCKET HEAD CAP SCREW x 12
92196A311_18-8 STAINLESS STEEL SOCKET HEAD CAP SCREW x 6

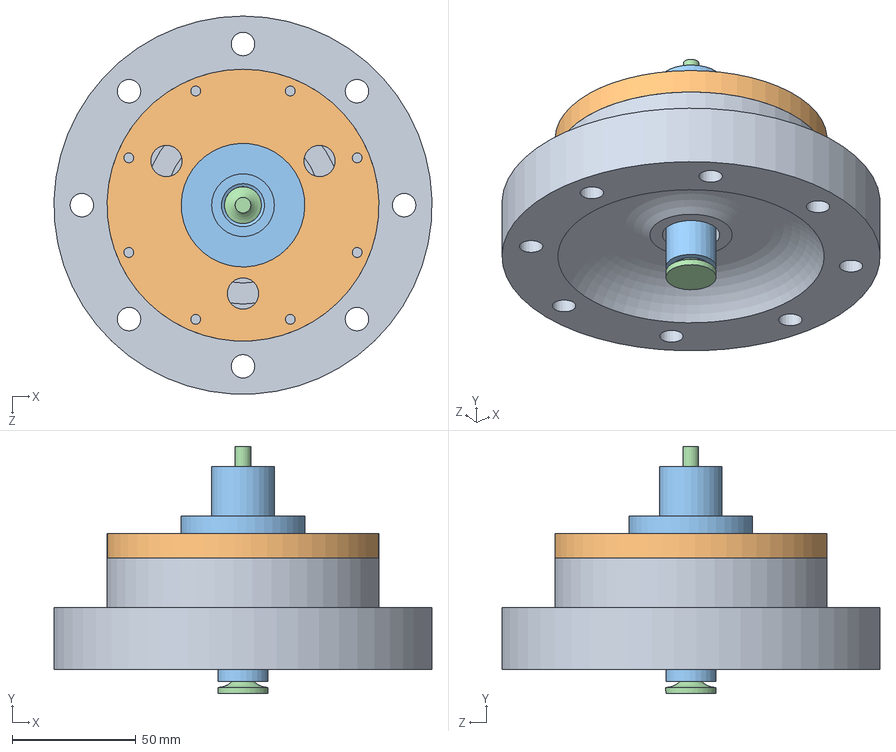
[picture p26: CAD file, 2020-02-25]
6kN Heat Sink Engine/SolidWorksFiles/LogRocket1.0/HeadUnitAssembly.SLDASM
152.9 x 100.0 x 152.9 mm
InjectorBaseV1
InjectorCapV1
Pintlev1
Pintle_CenterV1

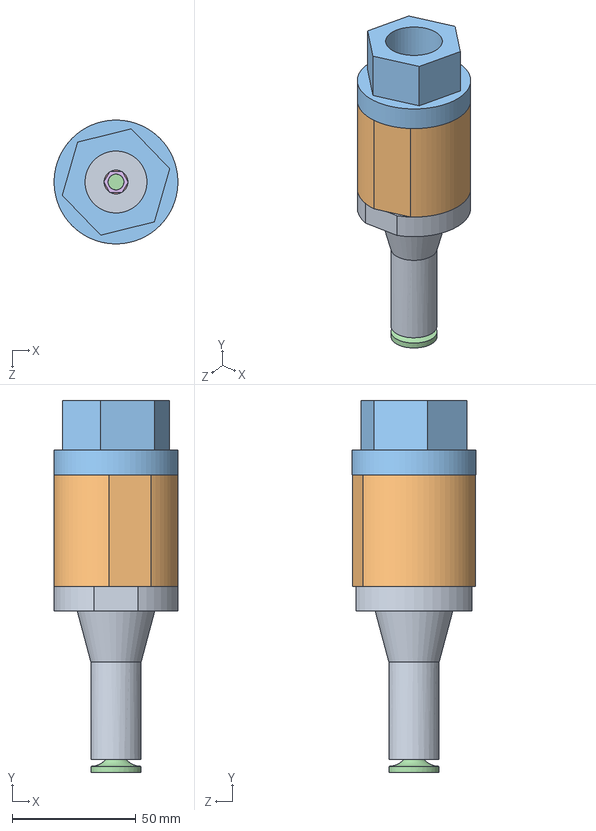
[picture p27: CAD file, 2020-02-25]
6kN Heat Sink Engine/SolidWorksFiles/LogRocketIdea/NewLoxPintleDesign.SLDASM
50.0 x 150.2 x 50.0 mm
Pintle_OuterV2
LOXaddapter
LOXin
Pintle_CenterV1
PintleWasher
PintleNut

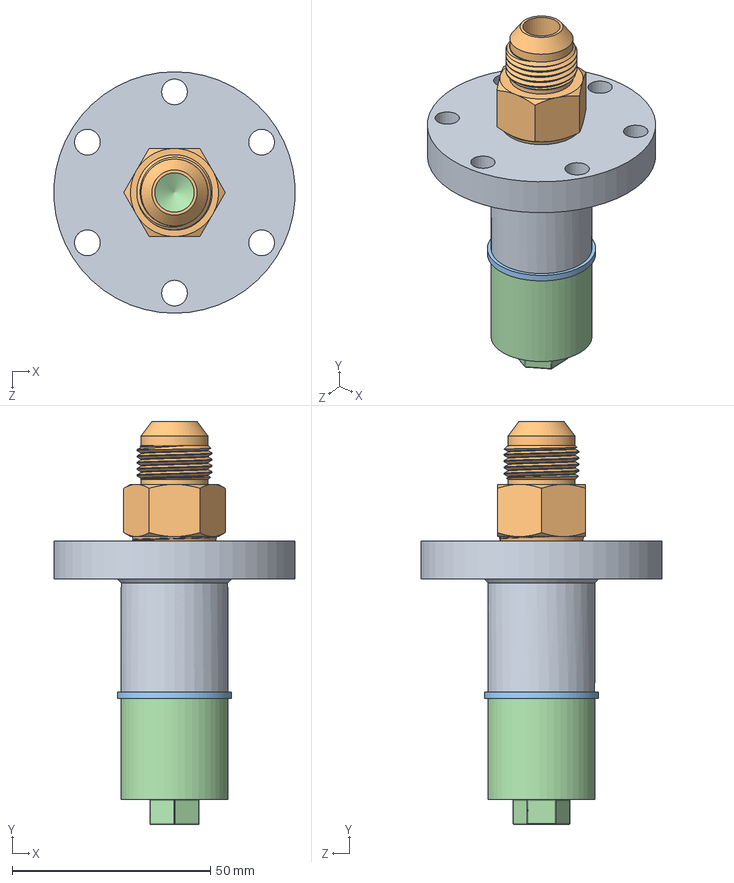
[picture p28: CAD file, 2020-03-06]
6kN Heat Sink Engine/SolidWorksFiles/LogRocketV7/pintleV7-4.sldasm
60.8 x 101.7 x 61.0 mm
pintleV7-4
5482K180_PRECISION AN 37 DEGREE FLARED TUBE FITTING
97725A123_METAL SEALING WASHER
pintle_tipV7-4
97725A590_METAL SEALING WASHER

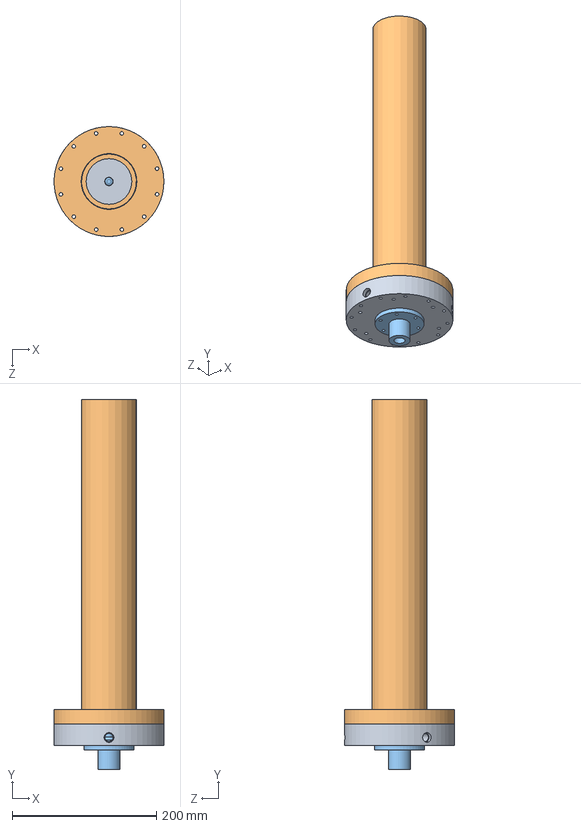
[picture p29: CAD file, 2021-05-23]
Throatless Test Stand Engine/ThroatlessStackup.SLDASM
152.4 x 513.3 x 152.4 mm
TopPlate
ThroatlessEngine
BasicPintle

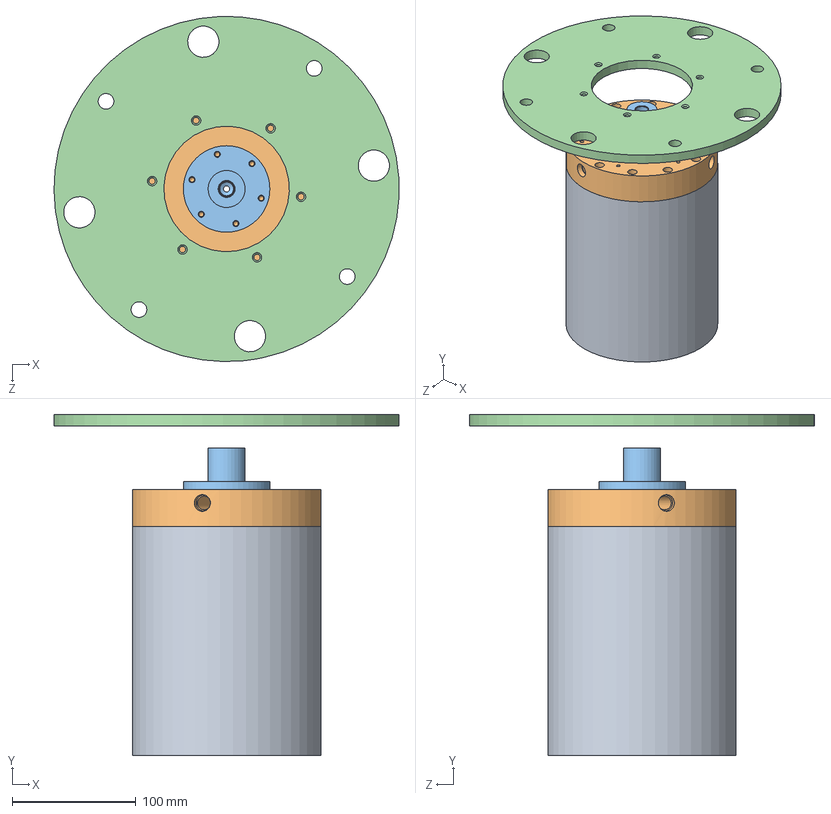
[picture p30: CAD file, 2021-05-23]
2kN Heat Sink Engine/Ready for Machining/FullStack1.SLDASM
279.2 x 276.3 x 279.3 mm
350psiEngineChamber
TopPlate
BasicPintle

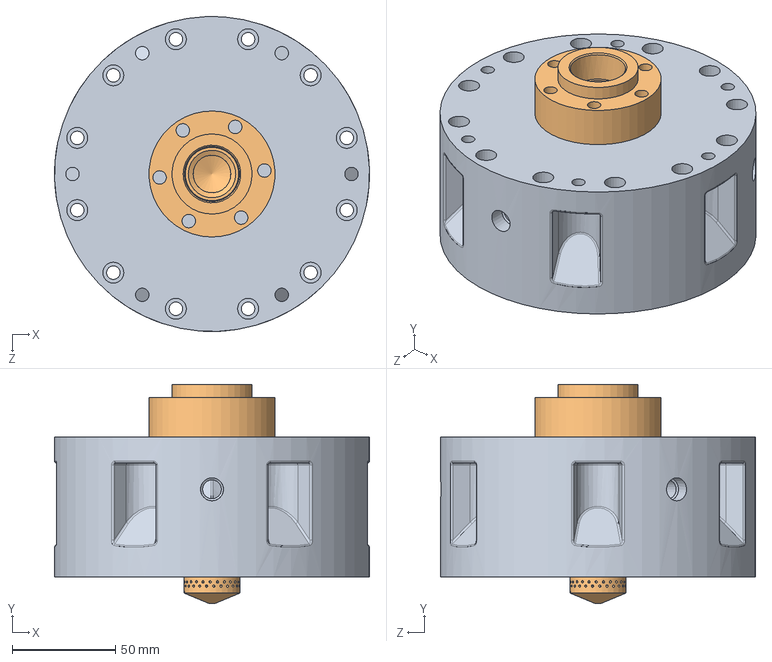
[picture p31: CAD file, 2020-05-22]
6kN Heat Sink Engine/SolidWorksFiles/hybridV2/Hybrid_Injector_forCFD.SLDASM
152.4 x 106.1 x 152.4 mm
injectorHead
pintleV7-5

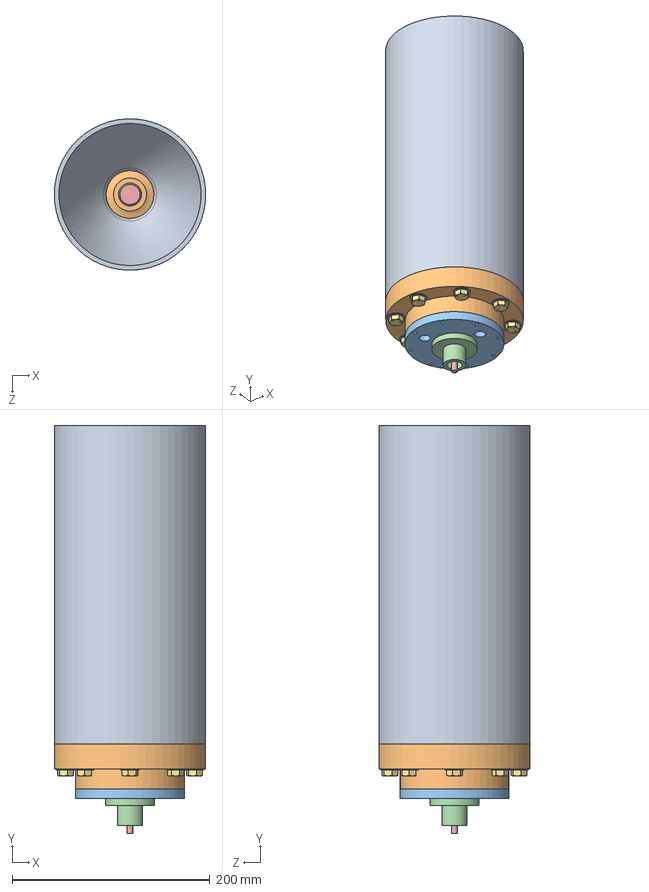
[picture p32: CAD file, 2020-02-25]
6kN Heat Sink Engine/SolidWorksFiles/LogRocket1.0/LogRocket_Built.SLDASM
153.0 x 412.3 x 152.9 mm
SolidRocket
InjectorBaseV1
InjectorCapV1
Pintlev1
Pintle_CenterV1
90107A127_TYPE 316 STAINLESS STEEL FLAT WASHER x 8
91247A223_MEDIUM-STRG GRADE 5 ZINC-PLTD STL CAP SCREW x 8

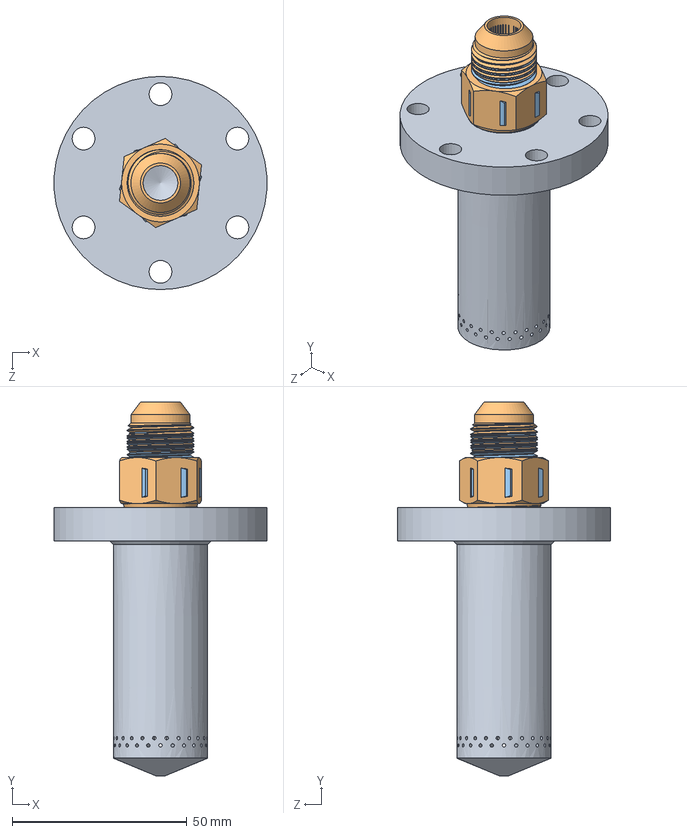
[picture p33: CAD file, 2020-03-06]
6kN Heat Sink Engine/SolidWorksFiles/LogRocketV7/pintleV7-5.SLDASM
60.8 x 106.9 x 61.0 mm
pintleV7-5
5482K180_PRECISION AN 37 DEGREE FLARED TUBE FITTING

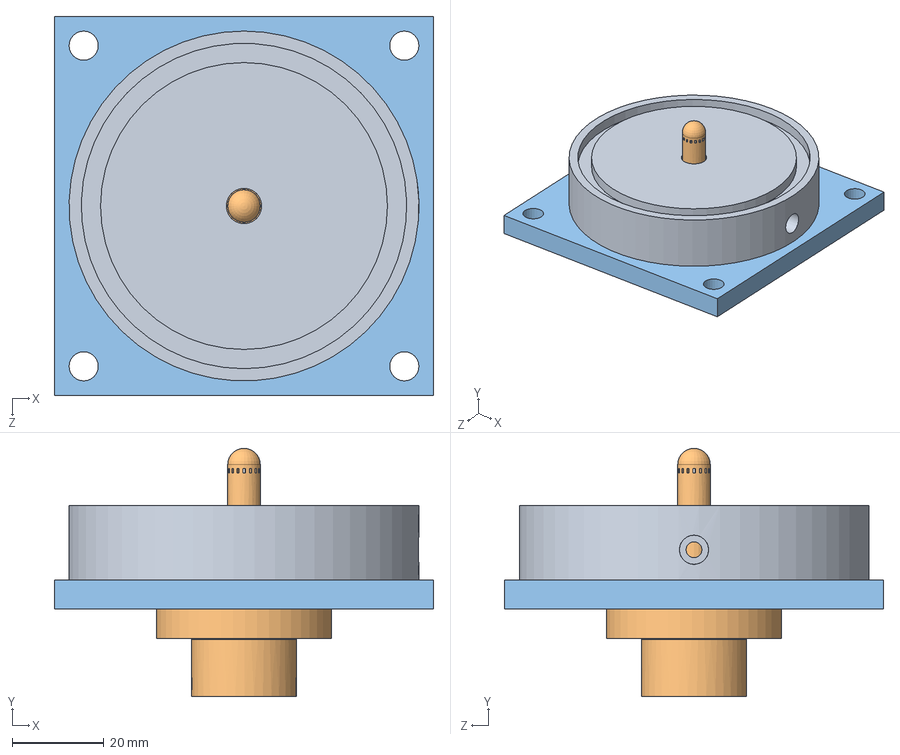
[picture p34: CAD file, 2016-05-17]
PintleDrawings/Assem_Water_Test_Weld_V7.SLDASM
82.5 x 54.1 x 82.5 mm
Test_Annulus_V7
pintle_V7_female_weld
SquarePlate

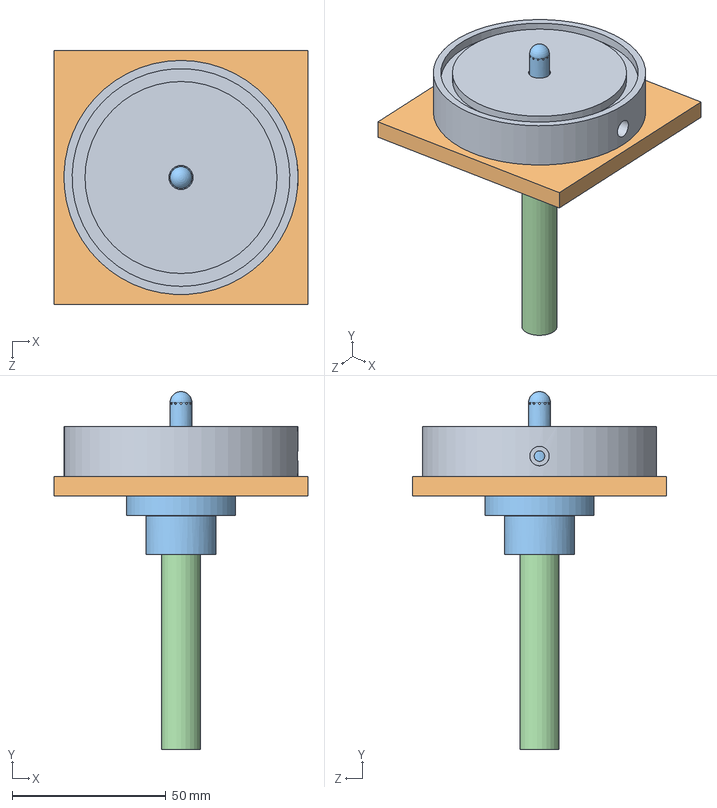
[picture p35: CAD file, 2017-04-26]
2kN/cad/PintleV1/Assembly_Cold_Test.SLDASM
82.5 x 116.5 x 82.5 mm
Part_Cold_Test_Annulus_V1
Part_Cold_Test_Plate_V1
Part_Pintle_V1
Part_SSTube

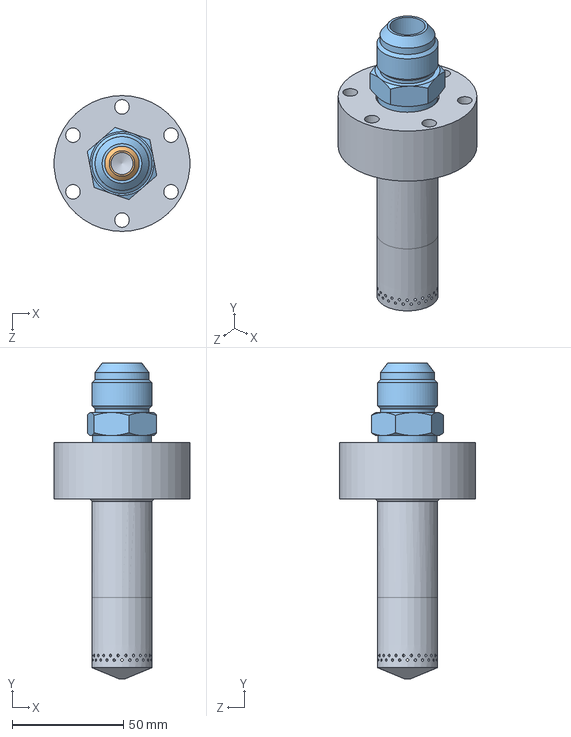
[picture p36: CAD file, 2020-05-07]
6kN Heat Sink Engine/SolidWorksFiles/hybridV2/pintleV7-5.SLDASM
60.8 x 141.8 x 61.0 mm
pintleV7-5
5482K126_PRECISION AN 37 DEGREE FLARED TUBE FITTING

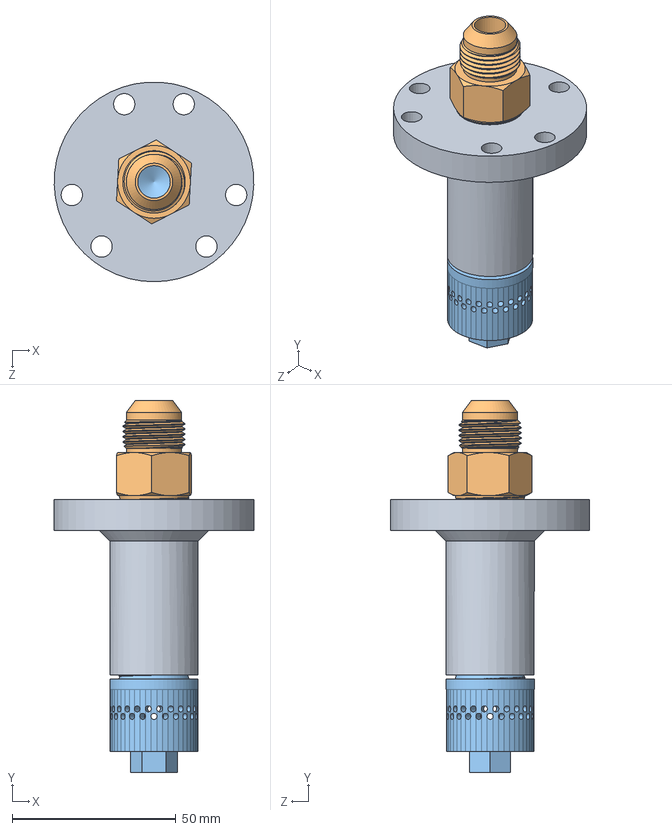
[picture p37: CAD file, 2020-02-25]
6kN Heat Sink Engine/SolidWorksFiles/LogRocketV7/pintleV7-3.SLDASM
60.9 x 113.6 x 60.9 mm
Pintle_OuterV8
5482K180_PRECISION AN 37 DEGREE FLARED TUBE FITTING
sprayer_tip

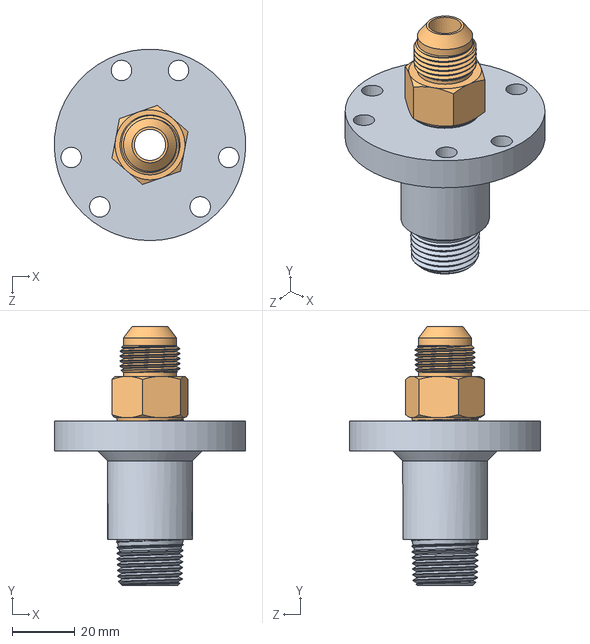
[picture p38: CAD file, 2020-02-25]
6kN Heat Sink Engine/SolidWorksFiles/LogRocketV7/pintleV7-2.SLDASM
60.9 x 82.5 x 60.9 mm
Pintle_OuterV7-2
5482K180_PRECISION AN 37 DEGREE FLARED TUBE FITTING

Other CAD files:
2kN Heat Sink Engine/Revised Stack OD 6in/FullStack1.SLDASM
6kN Heat Sink Engine/SolidWorksFiles/RoughRocketAssembly1.0/HeadUnitAssembly.SLDASM
6kN Heat Sink Engine/SolidWorksFiles/LogRocketV7/Pintle/Pintle_CenterV7.SLDASM
6kN Heat Sink Engine/SolidWorksFiles/LogRocketIdea/LogRocket_Built.SLDASM
2kN Heat Sink Engine/Ready for Machining/350psiEngineChamber.SLDPRT
2kN Heat Sink Engine/Ready for Machining/BasicPintle.SLDPRT
2kN Heat Sink Engine/Ready for Machining/BasicPintle.x_t
2kN Heat Sink Engine/Ready for Machining/BasicPintleInjector.SLDDRW
2kN Heat Sink Engine/Ready for Machining/PintleTopPlate.SLDDRW
2kN Heat Sink Engine/Ready for Machining/PintleTopPlate.x_t
2kN Heat Sink Engine/Ready for Machining/TopPlate.SLDPRT
2kN Heat Sink Engine/Revised Stack OD 6in/350psiEngineChamber.SLDPRT
2kN Heat Sink Engine/Revised Stack OD 6in/BasicPintle.SLDPRT
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

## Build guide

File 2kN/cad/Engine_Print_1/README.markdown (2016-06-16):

# 3D Prints Of The Nozzle

## June 8th 2016

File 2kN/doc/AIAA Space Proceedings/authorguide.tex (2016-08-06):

\maketitle
\end{Verbatim}

\subsection{Headings}

AIAA Technical Conferences style defines 3 levels of section
headings:
\begin{description}
 \item Level 1 heading (\verb"\section"): bold, larger font, centered,
       and numbered with Roman numerals.
 \item Level 2 heading (\verb"\subsection"): bold, flush left, and
       numbered with capital letters.  No opening paragraph indentation.
 \item Level 3 heading (\verb"\subsubsection"): italic, flush left, and
       numbered with Arabic numbers (e.g., 1, 2, 3).  No opening
       paragraph indentation.
\end{description}

\subsection{Abstract}

The abstract should appear at the beginning of your paper.
It should be one paragraph long (not an introduction) and complete in
itself (no reference numbers).
It should indicate subjects dealt with in the paper and state the
objectives of the investigation.
Newly observed facts and conclusions of the experiment or argument
discussed in the paper must be stated in summary form; readers should
not have to read the paper to understand the abstract.

\subsection{Footnotes and References}

Footnotes, where they appear, should be placed above the 1-inch margin at
the bottom of the page.
To insert footnotes, use \verb|\footnote{}| as normal.
Footnotes are formatted automatically in \verb|aiaa.cls|, but if
another medium is used, they should appear in as superscript lower case
letters.
When adding notes to tables, e.g., as accommodated by the
\pkg{threeparttable} package, the symbols are down by hand and should be
in the sequence, *, $\dagger$, $\ddagger$, $\mathsection$,
$\mathparagraph$, $\|$, **, $\dagger\dagger$, and so forth.
This sequence should beginning anew with each table.

List and number all bibliographical references at the end of the paper.
Corresponding superscript numbers are used to cite references in the
text using the \verb|\cite{}| command,\cite{sutton:85ar} unless the
citation is an integral part of the sentence (e.g., ``It is shown in
Ref.~\citen{miner:75ncr} that\ldots[.]'') 
or follows a mathematical expression: ``$A2 + B = C$
(Ref.~\citen{wirin:90cp}).''
For this case, the command, \verb|\citen{}| is used.
\cite{*}% to load all refences for demonstration purposes which follow
Multiple citations are sorted and punctuated automatically through the
\cls{aiaa-tc}'s use of the \pkg{overcite}. 
Separate reference numbers are shown with
commas\cite{sutton:85ar,miner:75ncr,turner:64a} and ranges are 
separated by an en-dash.\cite{sutton:85ar,miner:75ncr,wirin:90cp}
Reference citations in the text should be in numerical order, which is
assured by using \textsc{Bib}\TeX.

In the reference list, give all authors' names; do not use ``et al.''
unless there are six authors or more.
Papers that have not been published should be cited as ``unpublished'';
papers that have been submitted or accepted for publication should be
cited as ``submitted for publication.''
Private communications and personal Web sites should appear as footnotes
rather than in the reference list.

References should be cited according to the standard publication
reference style.
(For examples, see the ``References'' section of this template.)
This is facilitated by the Bib\TeX\ database and a style file, \file{aiaa.bst}.
As a rule, all words are capitalized except for articles, conjunctions,
and prepositions of four letters or fewer.
Names and locations of publishers should be listed; month and year
should be included for reports and papers.
For papers published in translation journals, please give the English
citation first, followed by the original foreign language citation.

\subsection{Images, Figures, and Tables}

All artwork, captions, figures, graphs, and tables will be reproduced
exactly as submitted.
Be sure to position any figures, tables, graphs, or pictures as you want
them printed.
AIAA is not responsible for incorporating your figures, tables,
etc.%
\footnote{Company logos and identification numbers are not permitted on
  your illustrations.}

% an experiment with wrapfig -- read caveats documented in wrapfig.sty
\begin{wrapfigure}{R}{0.5\linewidth}
 
 \caption{Magnetization as a function of applied field, which has
   borders so thick that they overwhelm the data and for some reason the
   ordinate label is rotated 90 degrees to make it difficult to
   read. This figure also demonstrates the dangers of using a bitmap
   as opposed to a vector image.}
 \label{f:magnetic_field}
\end{wrapfigure}

Place figure captions below all figures; place table titles above the
tables.%
\footnote{Please do not include captions as part of the figure image
itself.}
If your figure has multiple parts, include the labels ``a),'' ``b),''
and so on, below each subfigure and above the figure caption.
This can be accomplished with the \pkg{subfigure} package.
Please verify that the figures and tables you mention in the text
actually exist by using \LaTeX's \verb|\label| and \verb|\ref| mechanisms
and verifying that there are no undefined references during typesetting.

When citing a figure in the text, use ``figure'' as ``Fig., often used
to refer to graphics, is an ugly abbreviation and is not worth the two
spaces saved.''\cite{tufte:83bk}
Do not abbreviate ``table'' either.
Each different type of illustration (i.e., figures, tables, or
images) should be numbered sequentially with relation to other
illustrations of the same type.

Figure axis labels are often a source of confusion.
Use words rather than symbols.
As in the example to the right, write the quantity ``Magnetization''
rather than just ``M.''
Do not enclose units in parenthesis, but rather separate them from the
preceding text by commas.
Do not label axes only with units.
As in figure~\ref{f:magnetic_field}, for example, write ``Magnetization,
A/m'' or ``Magnetization, A m-1,'' not just ``A/m.''
Do not label axes with a ratio of quantities and units.
For example, write ``Temperature, K,'' not ``Temperature/K.''

Multipliers can be especially confusing.
Write ``Magnetization, kA/m'' or ``Magnetization, 103 A/m.''
Do not write ``Magnetization (A/m) $\times$ 1000'' because the reader
would not then know whether the top axis label in
figure~\ref{f:magnetic_field} meant 16000~A/m or 0.016~A/m.
Figure labels must be legible, approximately 8--12 point type.
Use of the \pkg{psfrag} package can facilitate this, but it makes
generating a PDF version of your paper difficult.

Figures and tables are referred to as `Floats' in \LaTeX, reflecting
their floating nature.
They are typically numbered whether or not they have a caption and they
are floated to the first available position near the first reference to
that figure/table within the text.
This is accomplished by placing the figure/table environment after
their first reference.
The environment can even be placed mid-sentence as long as \LaTeX's
comment character, \%, is used properly to prevent a paragraph break or
extra spaces.
By default, floats are placed at the top of the first available page,
the bottom of the page, or one a page consisting entirely of floats.

An example of coding a standard \verb|{figure}| is given below:
\begin{Verbatim}
 \begin{figure}
   
   \caption{Magnetization as a function of applied field, which has
     borders so thick that they overwhelm from the data.}
   \label{f:magnetic_field}
 \end{figure}
\end{Verbatim}

\begin{table}
 \begin{center}
  \begin{threeparttable}
   \caption{This is an example of a \pkg{threeparttable} which uses the
     \pkg{dcolumn} package to allow for columns to be aligned on decimal
     points.}
   \label{t:threepart}
   \begin{tabular}{lcdd}
    First head\tnote{*}  &
    Second head &
    \multicolumn{1}{c}{Third head} &
    \multicolumn{1}{c}{$V_M(r)$} \\\hline
    center & doctor &  0.2  & 10.55 \\  
    tab    & dentist &  0.15 & 33.12 \\ 
    worse  & man\tnote{\ensuremath{\dagger}} & 10.58 & 45.10 \\ 
    better & home & 43.9  & 12.34 \\
   \end{tabular}
   \begin{tablenotes}
    \item[*] This is a table footnote, which to span multiple lines, has
      been greatly extended in length contrary to reason.
    \item[\ensuremath{\dagger}] A much shorter table footnote.
   \end{tablenotes}
  \end{threeparttable}
 \end{center}
\end{table}
Tables with footnotes, such as table~\ref{t:threepart},
can be coded using the \pkg{threeparttable} package as follows:
\begin{Verbatim}
 \begin{table}
  \begin{center}
   \begin{threeparttable}
    \caption{This is an example of table caption.}
    \label{t:wordtable}
    \begin{tabular}{ccdd}
     First head\tnote{a}  &
     Second head\tnote{b} &
     \multicolumn{1}{c}{Third head} &
     \multicolumn{1}{c}{$V_M(r)$} \\\hline
     Left & Word entries &  0.2  & 10.55 \\  
     Left & Word entries &  0.15 & 33.12 \\ 
     Left & Word entries & 10.58 & 45.10 \\ 
     Left & Word entries & 43.9  & 12.34 \\
    \end{tabular}
    \begin{tablenotes}
     \item[a] This is a table footnote, which to span multiple lines, has
              been greatly extended in length contrary to reason.
     \item[b] A much shorter table footnote.
    \end{tablenotes}
   \end{threeparttable}
  \end{center}
 \end{table}
\end{Verbatim}

\subsection{Equations, Numbers, Symbols, and Abbreviations}

Equations are centered and numbered consecutively, with equation
numbers in parentheses flush right, as in Eq.~\ref{e:function}.
\begin{equation}
 \label{e:function}
 \int_{0}^{r_{2}} F(r,\varphi)\,dr\,d\varphi =
    \left[ \sigma r_{2}/(2\mu_{0}) \right] \cdot
    \int_{0}^{\infty} \exp(-\rho|z_{j}-z_{i}|) \lambda^{-1} 
\end{equation}
Equation~\ref{e:function} is coded as below:
\begin{Verbatim}
 \begin{equation}
  \label{e:function}
  \int_{0}^{r_{2}} F(r,\varphi)\,dr\,d\varphi =
     \left[ \sigma r_{2}/(2\mu_{0}) \right] \cdot
     \int_{0}^{\infty} \exp(-\rho|z_{j}-z_{i}|) \lambda^{-1}
 \end{equation}
\end{Verbatim}
A sample equation is included below, formatted using the preceding
instructions.
To make your equation more compact, you can use the solidus ($/$), the
exp function, or appropriate exponents.
Use parentheses to avoid ambiguities in denominators.
\begin{equation}
  \label{e:displace}
  \mathbf{J}_i\cdot\Delta\underline{x}_{i+1}=-\underline{f}_i
\end{equation}
\nomenclature{$J$}{Jacobian Matrix}
\nomenclature[b$i$]{$i$}{Variable number}
\nomenclature[g$\Delta$]{$\Delta x$}{Variable displacement vector}
\nomenclature{$f$}{Residual value vector}
\nomenclature{$x$}{Variable value vector}
\begin{equation}
  \label{e:newton}
  F=m\alpha
\end{equation}
\nomenclature{$F$}{Force, N}
\nomenclature{$m$}{Mass, kg}
\nomenclature[g$\alpha$]{$\alpha$}{Acceleration, m/s\textsuperscript{2}}

The \verb|fleqnarray| environment is used to display a sequence of
equations or inequalities. It is very much like a three-column
\verb|array| environment, with consecutive rows separated by
\verb|\\| and consecutive items within a row separated by an \&.
\begin{eqnarray}
&&\sum_{i\in H} p^0\cdot w^{0i}=\sum_i M^i (p^0) =
  \sum_i\left[p^0\cdot r^i + \sum_j \alpha^{ij} (p^0\cdot
  y^{0j})\right]\nonumber\\
&&{\qquad}= p^0 \cdot \sum_i r^i + p^0 \cdot \sum_i
\sum_i \alpha^{ij}
\end{eqnarray}
An equation number is placed on every line unless that line has a
\verb|\nonumber| command.

Be sure that the symbols in your equation are defined before the
equation appears, or immediately following.
In this case the \pkg{nomencl} package is used to automatically generate
the nomenclature section.

Italicize symbols ($T$ might refer to temperature, but T is the unit
Tesla).
Refer to ``Eq. (1),'' not ``(1)'' or ``equation (1)'' except at the
beginning of a sentence: ``Equation (1) is phat.''
Equations can be labeled other than ``Eq.'' should they represent
inequalities, matrices, or boundary conditions.
If what is represented is really more than one equation, the
abbreviation ``Eqs.'' can be used.

Define abbreviations and acronyms the first time they are used in the
text, even after they have already been defined in the abstract.
Very common abbreviations such as AIAA, SI, ac, and dc do not have to be
defined.
Abbreviations that incorporate periods should not have spaces: write
``P.R.,'' not ``P. R.''
Delete periods between initials if the abbreviation has three or more
initials; e.g., U.N. but ESA.\@
Do not use abbreviations in the title unless they are unavoidable (for
instance, ``AIAA'' in the title of this article).

\subsection{General Grammar and Preferred Usage}

Use only one space after periods or colons. Hyphenate complex
modifiers: ``zero-field-cooled magnetization.''
Avoid dangling participles, such as, ``Using Eq. (1), the potential was
calculated.''
[It is not clear who or what used Eq. (1).]
Write instead ``The potential was calculated using Eq. (1),'' or ``Using
Eq. (1), we calculated the potential.''

Use a zero before decimal points: ``0.25,'' not ``.25.''
Use ``cm$^3$,'' not ``cc.''
Indicate sample dimensions as ``0.1 cm $\times$ 0.2 cm,'' not ``0.1
$\times$ 0.2~cm$^2$.''
The preferred abbreviation for ``seconds'' is ``s,'' not ``sec.''
Do not mix complete spellings and abbreviations of units: use
``Wb/m$^2$'' or ``webers per square meter,'' not ``webers/m$^2$.''
When expressing a range of values, write ``7 to 9'' or ``7--9,'' not
``7~9.''

A parenthetical statement at the end of a sentence is punctuated
outside of the closing parenthesis (like this).
(A parenthetical sentence is punctuated within parenthesis.)
In American English, periods and commas are placed within quotation
marks, like ``this period.''
Other punctuation is ``outside''! Avoid contractions; for example, write
``do not'' instead of ``don't.''
The serial comma is preferred: ``A, B, and C'' instead of ``A, B and C.''

If you wish, you may write in the first person singular or plural and
use the active voice (``I observed that\ldots'' or ``We observed that\ldots''
instead of ``It was observed thatÖ'').
Remember to check spelling.
If your native language is not English, please ask a native
English-speaking colleague to proofread your paper.

The word ``data'' is plural, not singular (i.e., ``data are,'' not ``data
is'').
The subscript for the permeability of vacuum $\mu_0$ is zero, not a
lowercase letter ``oo.''
The term for residual magnetization is ``remanence''; the adjective is
``remanent''; do not write ``remnance'' or ``remnant.''
The word ``micrometer'' is preferred over ``micron'' when spelling out
this unit of measure.
A graph within a graph is an ``inset,'' not an ``insert.''
The word ``alternatively'' is preferred to the word ``alternately''
(unless you really mean something that alternates).
Use the word ``whereas'' instead of ``while'' (unless you are referring
to simultaneous events).
Do not use the word ``essentially'' to mean ``approximately'' or
``effectively.''
Do not use the word ``issue'' as a euphemism for ``problem.''
When compositions are not specified, separate chemical symbols by
en-dashes; for example, ``NiMn'' indicates the intermetallic compound
Ni$_{0.5}$Mn$_{0.5}$ whereas ``Ni--Mn'' indicates an alloy of some
composition Ni$_{x}$Mn$_{1-x}$.

Be aware of the different meanings of the homophones ``affect'' (usually
a verb) and ``effect'' (usually a noun), ``complement'' and
``compliment,'' ``discreet'' and ``discrete,'' ``principal'' (e.g.,
``principal investigator'') and ``principle'' (e.g., ``principle of
measurement''). Do not confuse ``imply'' and ``infer.''

Prefixes such as ``non,'' ``sub,'' ``micro,'' ``multi,'' and ``ultra''
are not independent words; they should be joined to the words they
modify, usually without a hyphen.
There is no period after the ``et'' in the abbreviation ``et al.''
The abbreviation ``i.e.,'' means ``that is,'' and the abbreviation
``e.g.,'' means ``for example'' (these abbreviations are not
italicized).
An excellent source of more detailed style and formatting instructions
can be found in the AIAA style guide, {\it AIAA Style} (available from AIAA
upon request).

\section{Conclusion}

A conclusion section is not required, though it is preferred.
Although a conclusion may review the main points of the paper, do not
replicate the abstract as the conclusion.
A conclusion might elaborate on the importance of the work or suggest
applications and extensions.%
\footnote{The conclusion section is the last section of
  the paper that should be numbered.
  The appendix (if present), acknowledgment, and references should be
  listed without numbers.}

\section*{Appendix}

An appendix, if needed, should appear before the acknowledgments.
Use the 'starred' version of the \verb|\section| commands to avoid
section numbering.

\section*{Acknowledgments}

The preferred spelling of the word ``acknowledgment'' in American
English is without the ``e'' after the ``g.''
Avoid expressions such as ``One of us (S.B.A.) would like to thank\ldots[.]''
Instead, write ``F. A. Author thanks\ldots[.]''
Sponsor and financial support acknowledgments are also to be listed in
the acknowledgments section.

% produces the bibliography section when processed by BibTeX
\bibliography{bibtex_database}
\bibliographystyle{aiaa}

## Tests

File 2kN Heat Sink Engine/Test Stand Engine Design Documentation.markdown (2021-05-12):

# Design Documentation for the 2kN Heat Sink Engine #

In an attempt to wrangle some design requirements into a single location, this document is to serve as a first-location reference for design variables and documentation.

## Basic Parameters ##

* Thrust: 500lbf (2.2kN)
* Chamber Pressure: 350psia (2.41 MPa)
* Exit Pressure: 14.7 psia (0.101 MPa)
* Oxidizer: Liquid Oxygen
* Fuel: Isopropyl alcohol, 70% by volume *(Note: this is 64.8% IPA, 35.2% water by mass, according to my calculations)*
* Holes in the pintle exit cannot intersect

## Injector Parameters ##

### Flowrates:
* Fuel: 0.87 lb/sec (0.394 kg/sec)
* Oxidizer: 1.13 lb/sec (0.513 kg/sec)
* Total: 2.0 lb/sec (0.907 kg/sec)
* Momenta of fuels should be equal

*(Note: these values are from the PSAS LFE python notebook scripts. May vary slightly if using RPA to calculate flowrates.)*
	
### Pressure Loss ###

* Pressure loss target = 70 psi (483 kPa) for Pintle and Annulus

Pressure target for the injector is 20% of the chamber pressure. This is not a precise target and sourcing is pretty sketchy, so this is a somewhat squishy number, however with a 350psi chamber pressure, we are shooting for 70 psi (483 kPa) pressure loss through the injector. There is more discussion in Jacob Tiller's pintle documentation, however the general idea is there needs to be enough pressure drop to accelerate the fluids and cushion upstream from combustion instability, but there is a clear upper limit created by the cavitating venturis upstream of the injector.

### Fluid Velocities ###

* The fluid velocity target range is ~30-100 ft/s (~10-30 m/s, 360-1200 in/s). 

This is a range from recollection. This value can be found by calculated from flowrates & total orifice areas. This value is necessary to calculate the momentum ratio, which helps define the combination fan angle of the fluids. 

Bonus points if you can find the sourcing for this information. Marc has lost it... if you do, please add reference here. Probably can be found in Huzel & Huang. 

### Momentum Ratio ###

* The target momentum ratio for the injector is 1:1

Fluid momentum is mdot*V, as explained in Jacob Tiller's pintle documentation. The momentum ratio of the fluids dictates the combined angle of the flow from the axial fuel and radial oxidizer flows. The target angle is 45 degrees, corresponding to a 1:1 momentum ratio.

## Strategy ##

CAD design strategy here...

## Reference

The "Jacob Tiller" document referenced above can be found [HERE](https://github.com/psas/pintle-injector/blob/master/Pintle%20Injector%20Design%20Documentation/00%20-%20Pintle%20Injector%20Theory%2C%20Design%2C%20and%20Testing.ipy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)

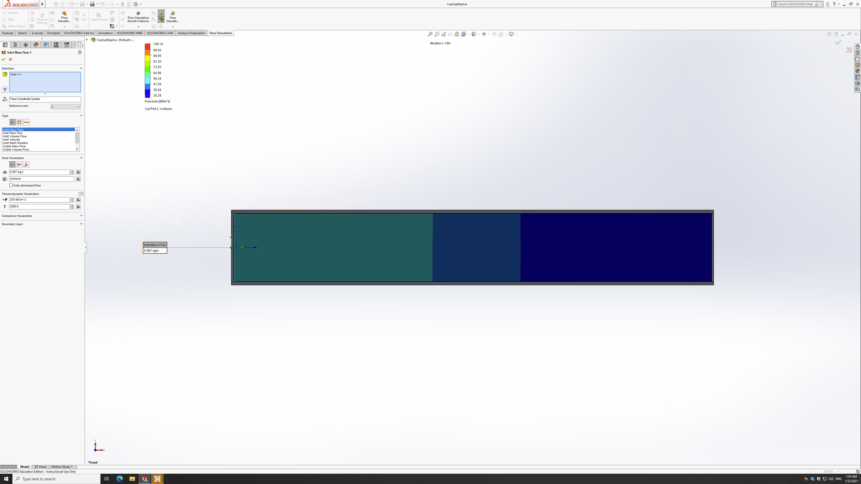
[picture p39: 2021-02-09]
Throatless Test Stand Engine/throatless/Sim Pressures/Screen Shot 2021-01-22 at 1.45.07 AM.png

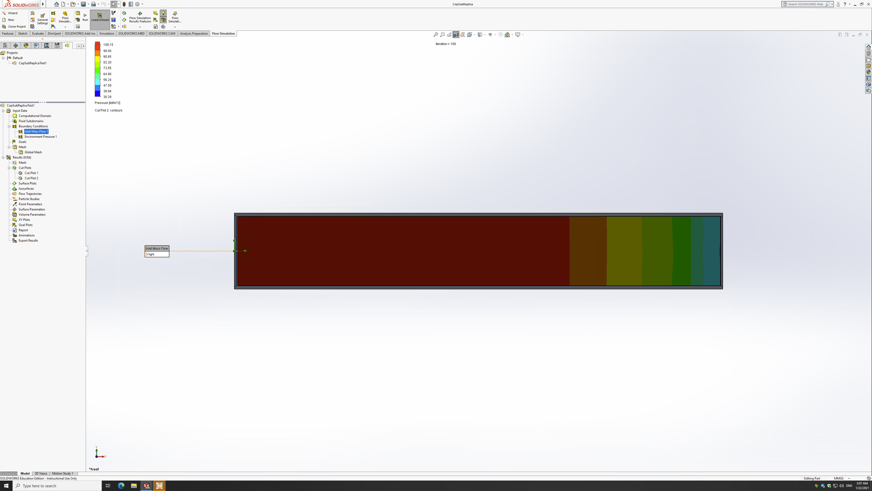
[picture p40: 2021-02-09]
Throatless Test Stand Engine/throatless/Sim Pressures/Screen Shot 2021-01-22 at 2.07.36 AM.png

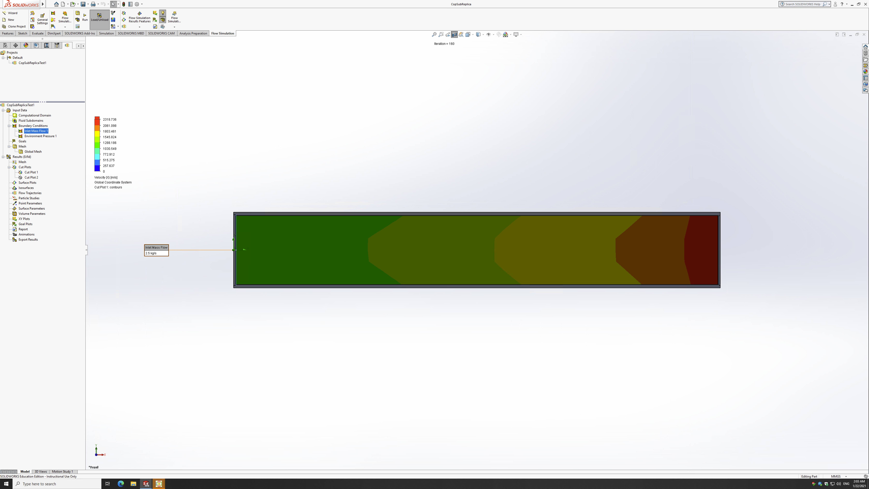
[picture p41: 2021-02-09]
Throatless Test Stand Engine/throatless/Sim Velocities/Screen Shot 2021-01-22 at 2.03.56 AM.png

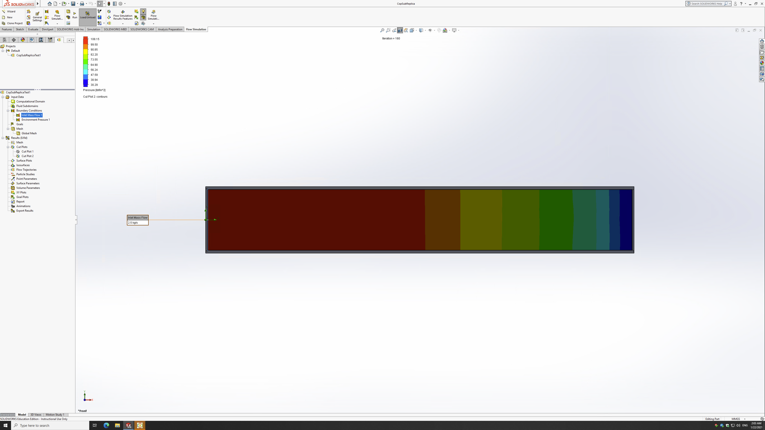
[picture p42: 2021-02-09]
Throatless Test Stand Engine/throatless/Sim Pressures/Screen Shot 2021-01-22 at 2.03.40 AM.png

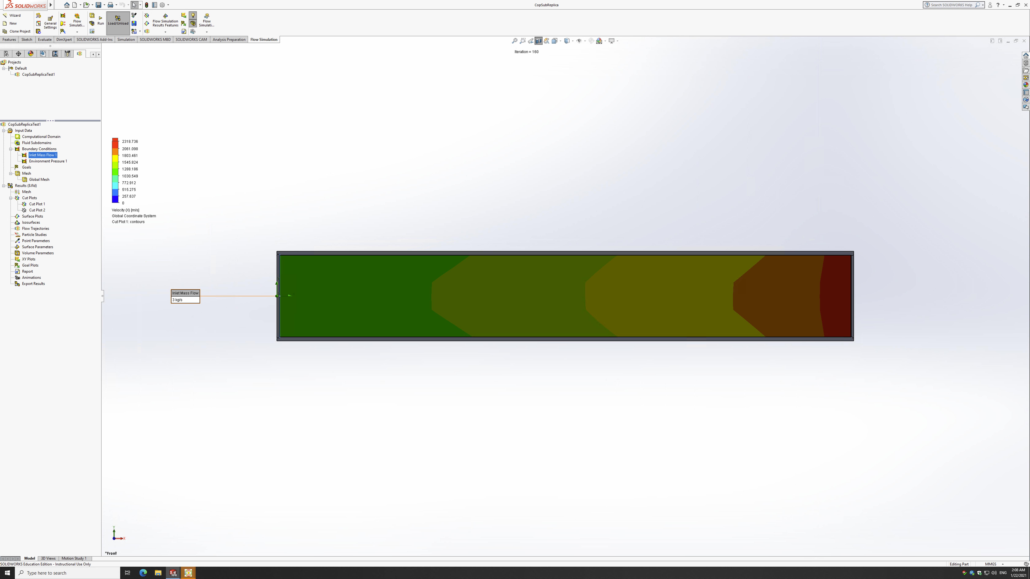
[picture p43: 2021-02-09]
Throatless Test Stand Engine/throatless/Sim Velocities/Screen Shot 2021-01-22 at 2.08.02 AM.png

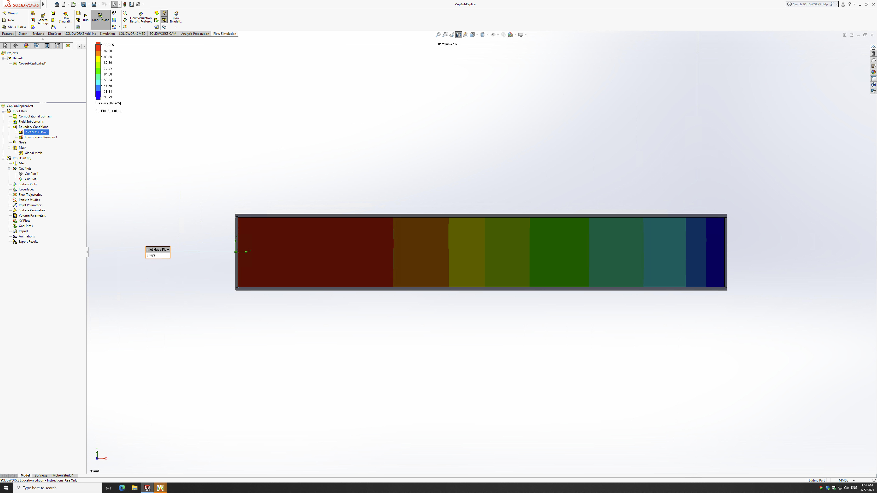
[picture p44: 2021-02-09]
Throatless Test Stand Engine/throatless/Sim Pressures/Screen Shot 2021-01-22 at 1.57.04 AM.png

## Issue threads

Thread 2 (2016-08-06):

Update Mass Flow Rates For Aluminum Design

Blueorchid, 2016-08-06:
Hi, at some point we need to update the mass flow rates to match the new aluminum design.

Total propellant flow rate: 2.06 lb/s
Ethanol flow rate: 0.94 lb/s
LOX flow rate: 1.13 lb/s

Not sure if it would be beneficial to combine the injector and the nozzle Jupyter notebooks into one someday, or keep them separate.

7deeptide, 2016-08-07:
I suggest keeping the the notebooks separate. However it would be really beneficial to add notes on motivation and workflow to the git readme.

The gps board repo is an exemplar of a quality readme:
https://github.com/psas/gps-rf-board

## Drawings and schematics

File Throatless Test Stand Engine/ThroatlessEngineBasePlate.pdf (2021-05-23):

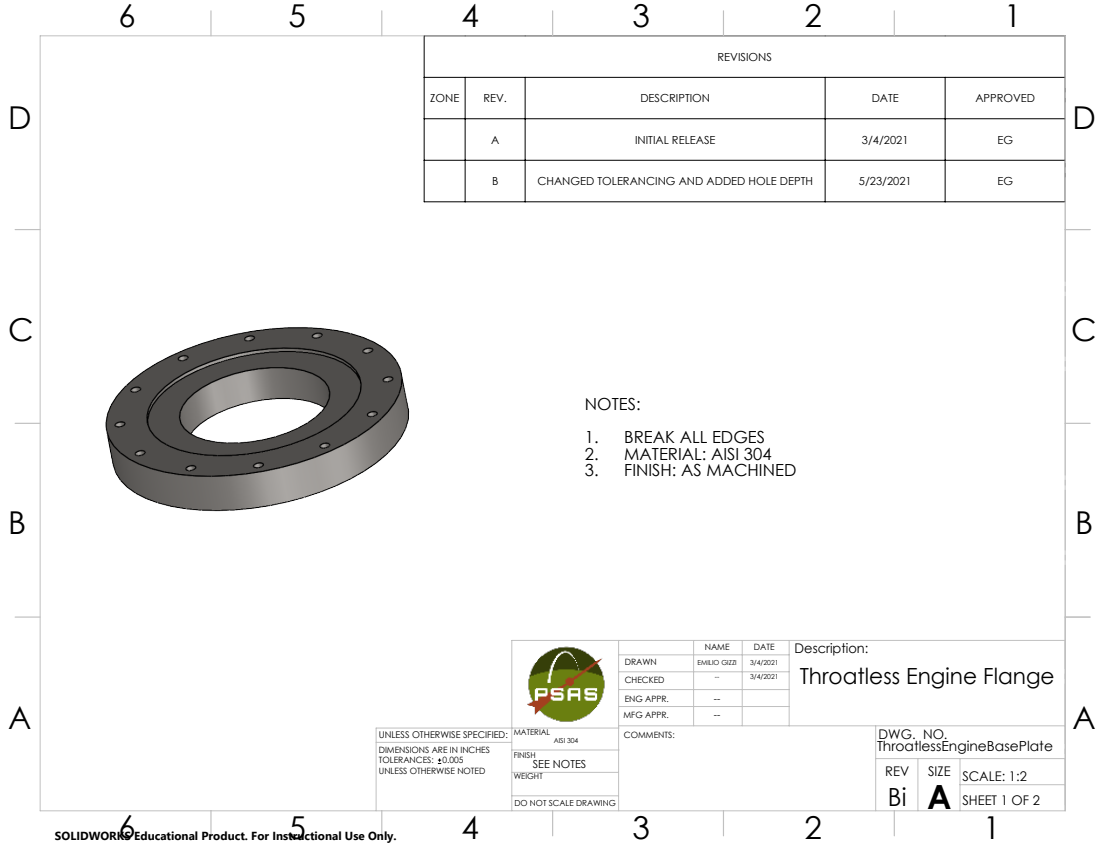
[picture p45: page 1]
REV; SCALE: 1:2; DO NOT SCALE DRAWING; SHEET 1 OF 2; SEE NOTES

REVISIONS

ZONE | REV. | DESCRIPTION | DATE | APPROVED

A | INITIAL RELEASE | 3/4/2021 | EG

B | CHANGED TOLERANCING AND ADDED HOLE DEPTH | 5/23/2021 | EG

NOTES:
1. BREAK ALL EDGES
2. MATERIAL: AISI 304
3. FINISH: AS MACHINED

NAME | DATE | Description: Throatless Engine Flange

DRAWN | EMILIO GIZZI | 3/4/2021
CHECKED | -- | 3/4/2021
ENG APPR. | --
MFG APPR. | --

UNLESS OTHERWISE SPECIFIED: | MATERIAL AISI 304 | COMMENTS: | DWG. NO. ThroatlessEngineBasePlate

DIMENSIONS ARE IN INCHES
TOLERANCES: 0.005
UNLESS OTHERWISE NOTED

SOLIDWORKS Educational Product. For Instructional Use Only.

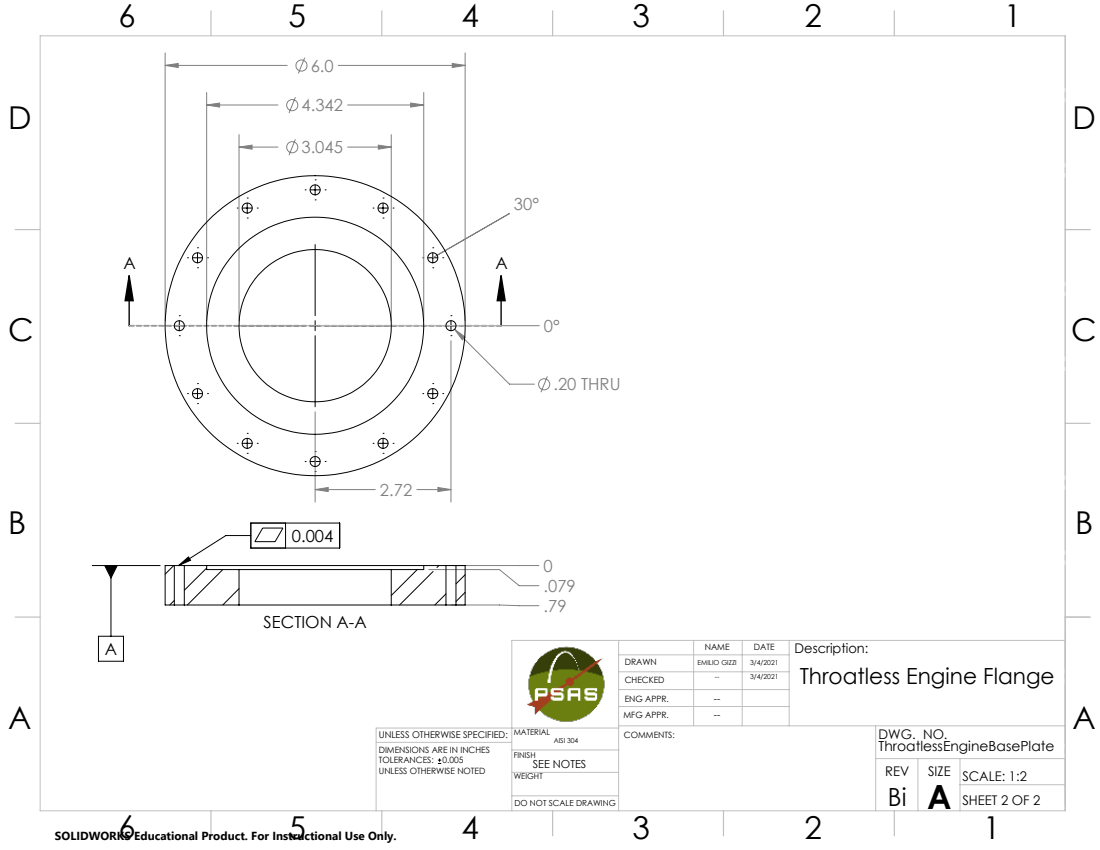
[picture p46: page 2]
.20 THRU; SECTION A-A; REV; SCALE: 1:2; DO NOT SCALE DRAWING; SHEET 2 OF 2; SEE NOTES

NAME | DATE | Description: Throatless Engine Flange

DRAWN | EMILIO GIZZI | 3/4/2021
CHECKED | -- | 3/4/2021
ENG APPR. | --
MFG APPR. | --

UNLESS OTHERWISE SPECIFIED: | MATERIAL AISI 304 | COMMENTS: | DWG. NO. ThroatlessEngineBasePlate

DIMENSIONS ARE IN INCHES
TOLERANCES: 0.005
UNLESS OTHERWISE NOTED

SOLIDWORKS Educational Product. For Instructional Use Only.

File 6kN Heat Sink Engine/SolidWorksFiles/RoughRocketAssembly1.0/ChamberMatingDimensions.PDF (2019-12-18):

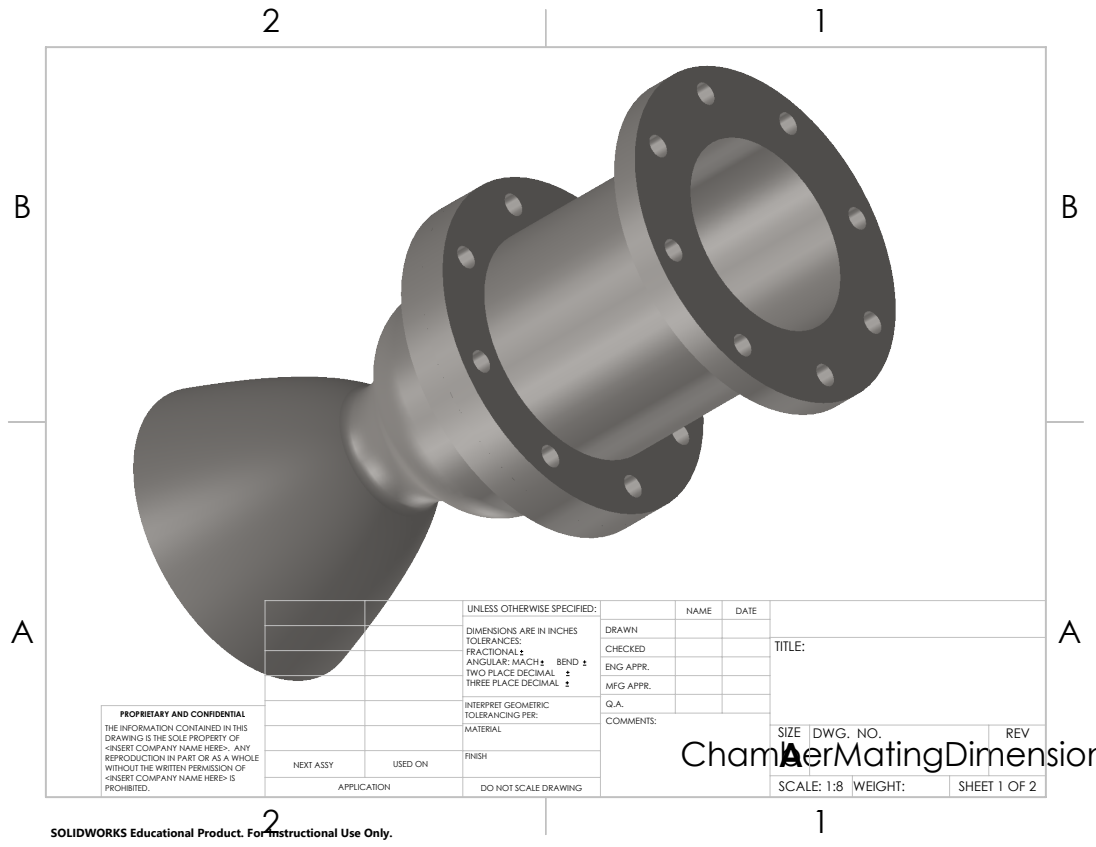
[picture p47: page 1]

UNLESS OTHERWISE SPECIFIED: | | NAME | DATE
DIMENSIONS ARE IN INCHES TOLERANCES: FRACTIONAL ANGULAR: MACH BEND TWO PLACE DECIMAL THREE PLACE DECIMAL | DRAWN

CHECKED | | | TITLE:

ENG APPR.
MFG APPR.

INTERPRET GEOMETRIC TOLERANCING PER: | Q.A.
MATERIAL | | SIZE A | DWG. NO. | REV

PROPRIETARY AND CONFIDENTIAL
THE INFORMATION CONTAINED IN THIS
DRAWING IS THE SOLE PROPERTY OF
<INSERT COMPANY NAME HERE>. ANY
REPRODUCTION IN PART OR AS A WHOLE
WITHOUT THE WRITTEN PERMISSION OF
<INSERT COMPANY NAME HERE> IS
PROHIBITED.

NEXT ASSY | USED ON | FINISH

APPLICATION | DO NOT SCALE DRAWING | | SCALE: 1:8 | WEIGHT: | SHEET 1 OF 2

SOLIDWORKS Educational Product. For Instructional Use Only.

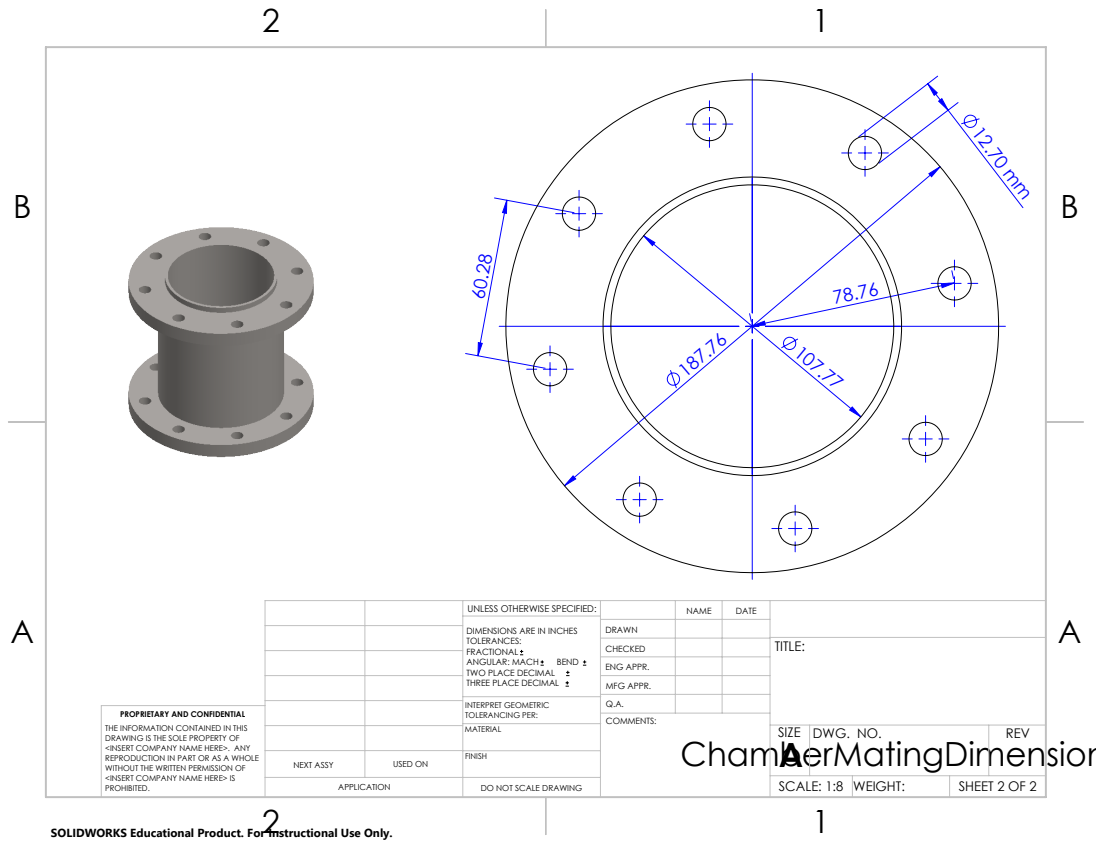
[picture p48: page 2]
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

CHECKED | | | TITLE:

ENG APPR.
MFG APPR.

INTERPRET GEOMETRIC TOLERANCING PER: | Q.A.
MATERIAL | | SIZE A | DWG. NO. | REV

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

NEXT ASSY | USED ON | FINISH

APPLICATION | DO NOT SCALE DRAWING | | SCALE: 1:8 | WEIGHT: | SHEET 2 OF 2

SOLIDWORKS Educational Product. For Instructional Use Only.

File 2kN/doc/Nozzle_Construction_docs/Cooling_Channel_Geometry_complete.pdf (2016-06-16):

# Cooling Channel Geometry

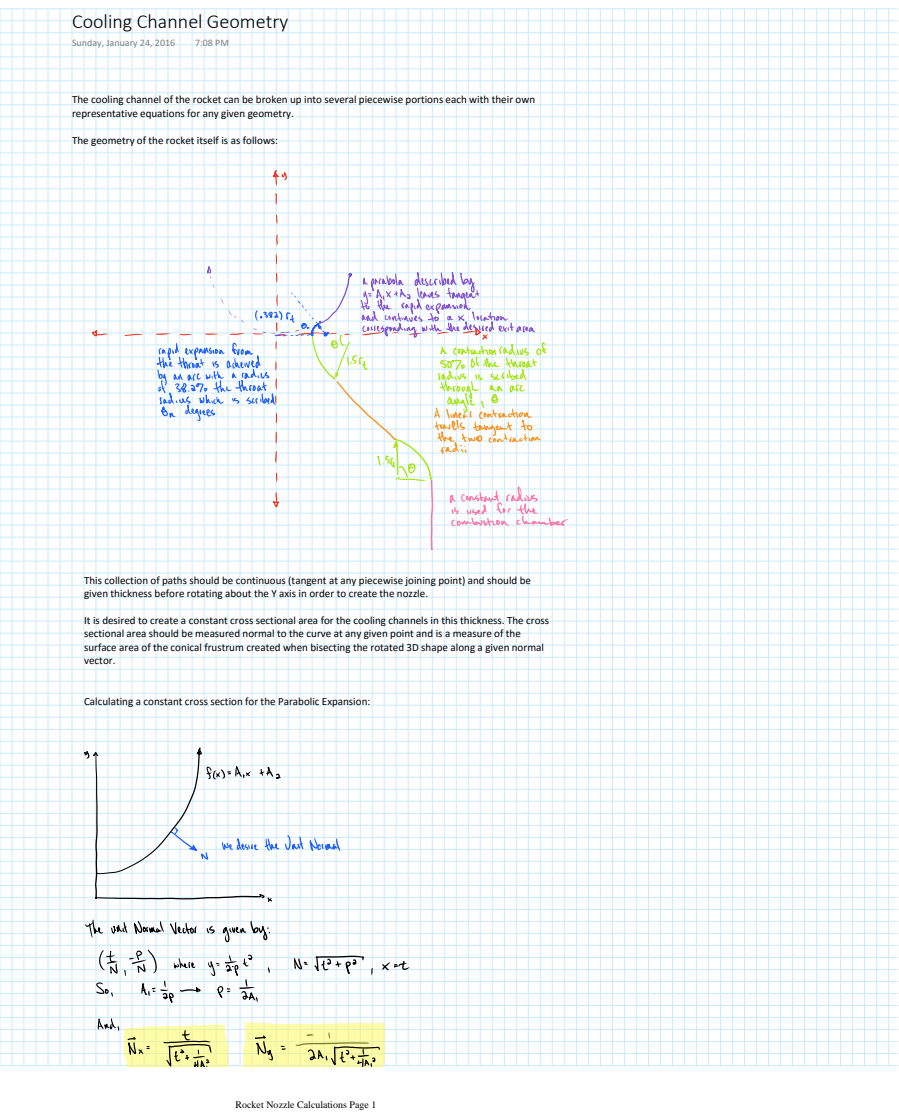
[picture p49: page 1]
Sunday, January 24, 2016

The cooling channel of the rocket can be broken up into several piecewise portions each with their own
representative equations for any given geometry.

The geometry of the rocket itself is as follows:

This collection of paths should be continuous (tangent at any piecewise joining point) and should be
given thickness before rotating about the Y axis in order to create the nozzle.

It is desired to create a constant cross sectional area for the cooling channels in this thickness. The cross
sectional area should be measured normal to the curve at any given point and is a measure of the
surface area of the conical frustrum created when bisecting the rotated 3D shape along a given normal
vector.

Calculating a constant cross section for the Parabolic Expansion:

Rocket Nozzle Calculations Page 1

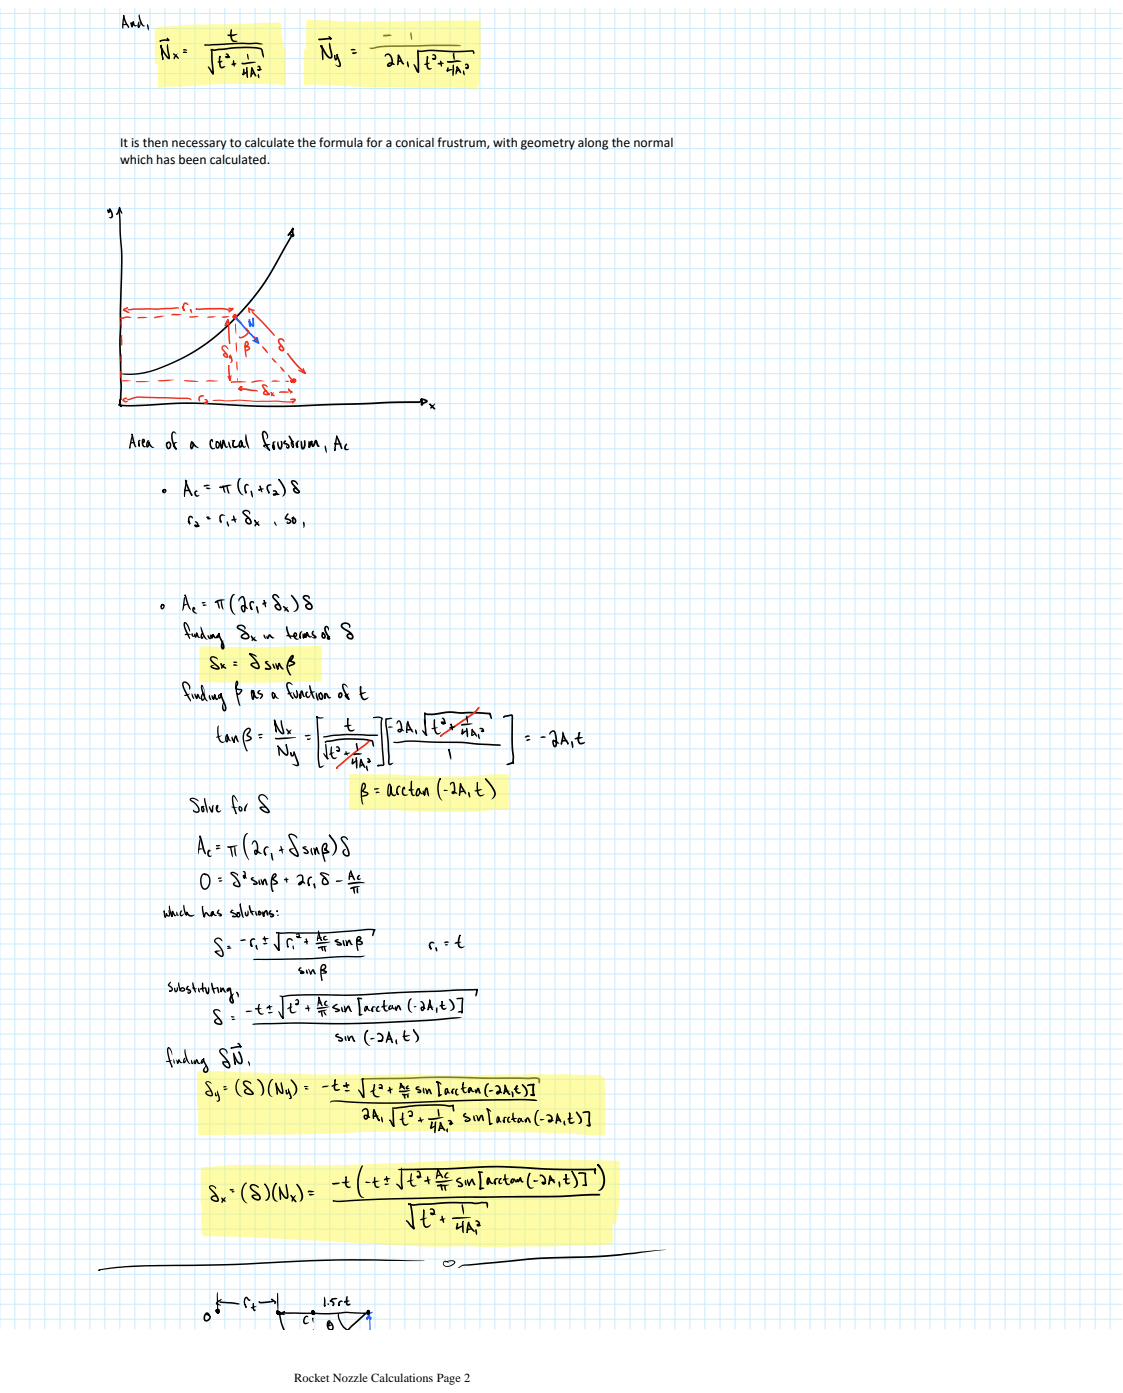
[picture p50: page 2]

It is then necessary to calculate the formula for a conical frustrum, with geometry along the normal
which has been calculated.

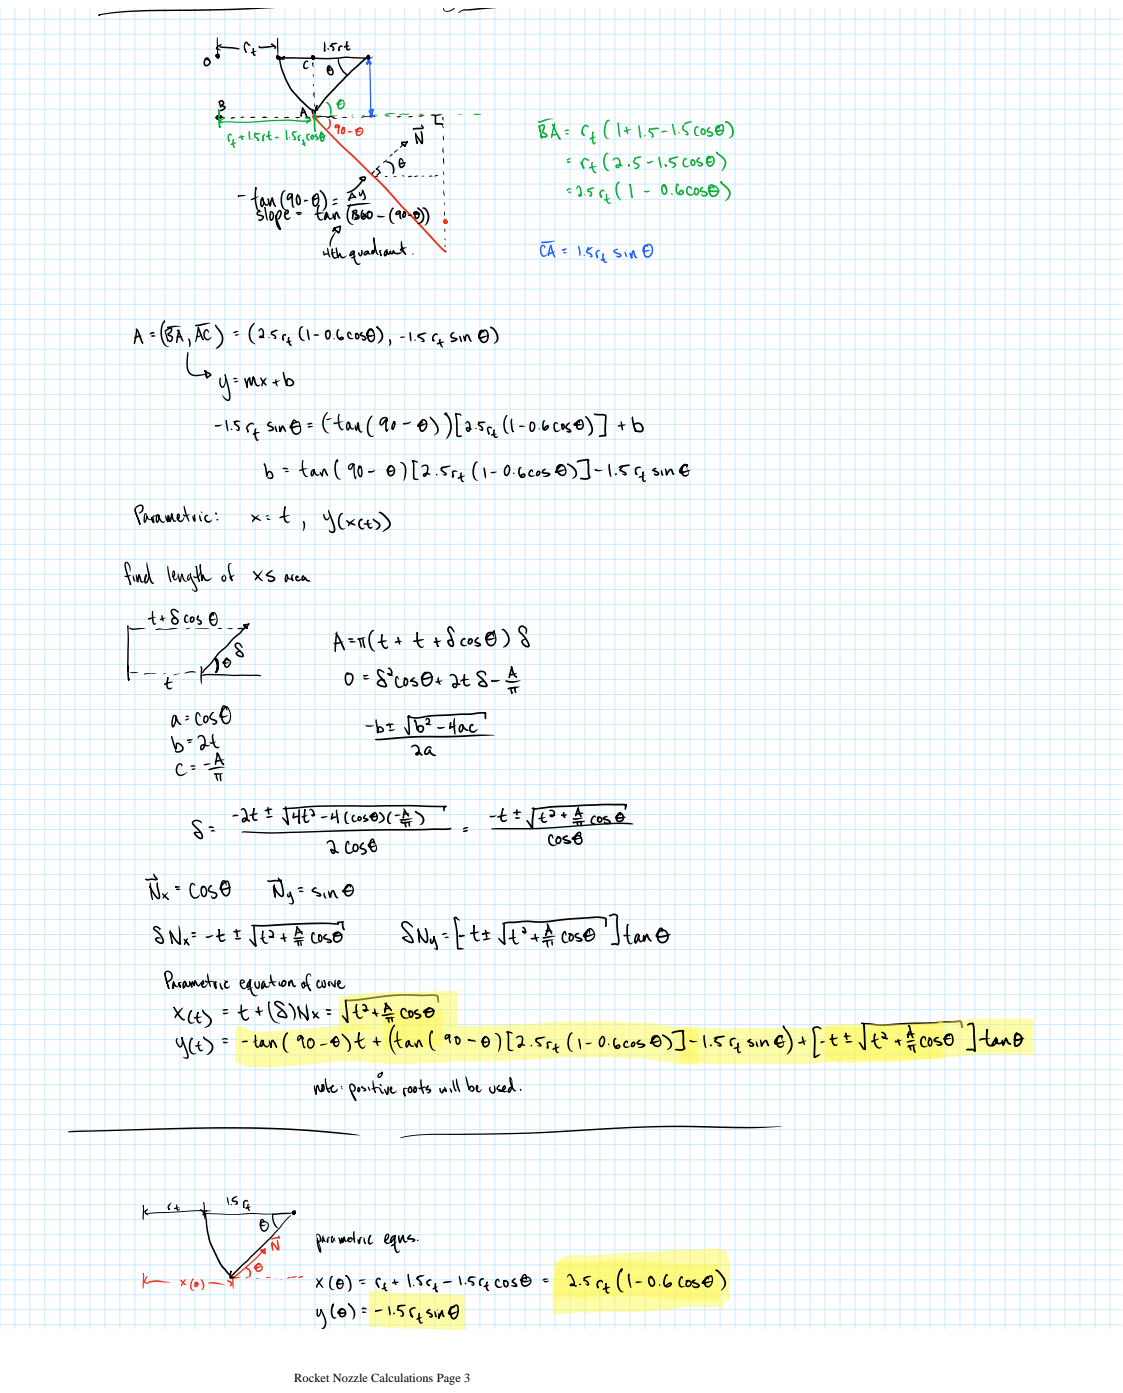
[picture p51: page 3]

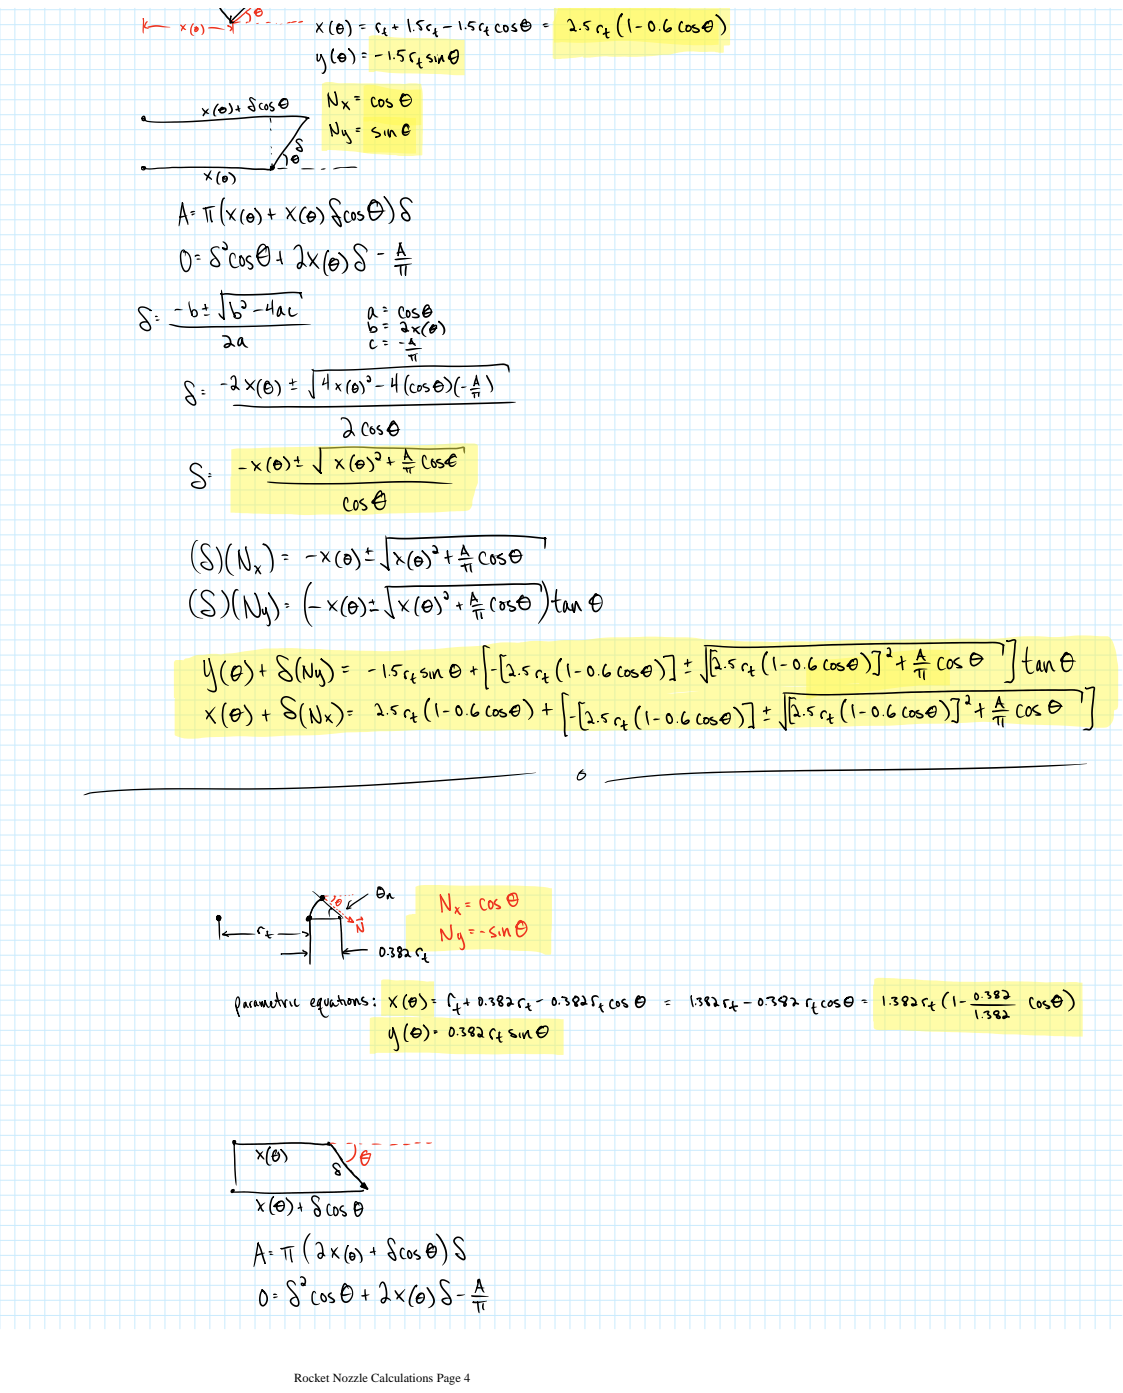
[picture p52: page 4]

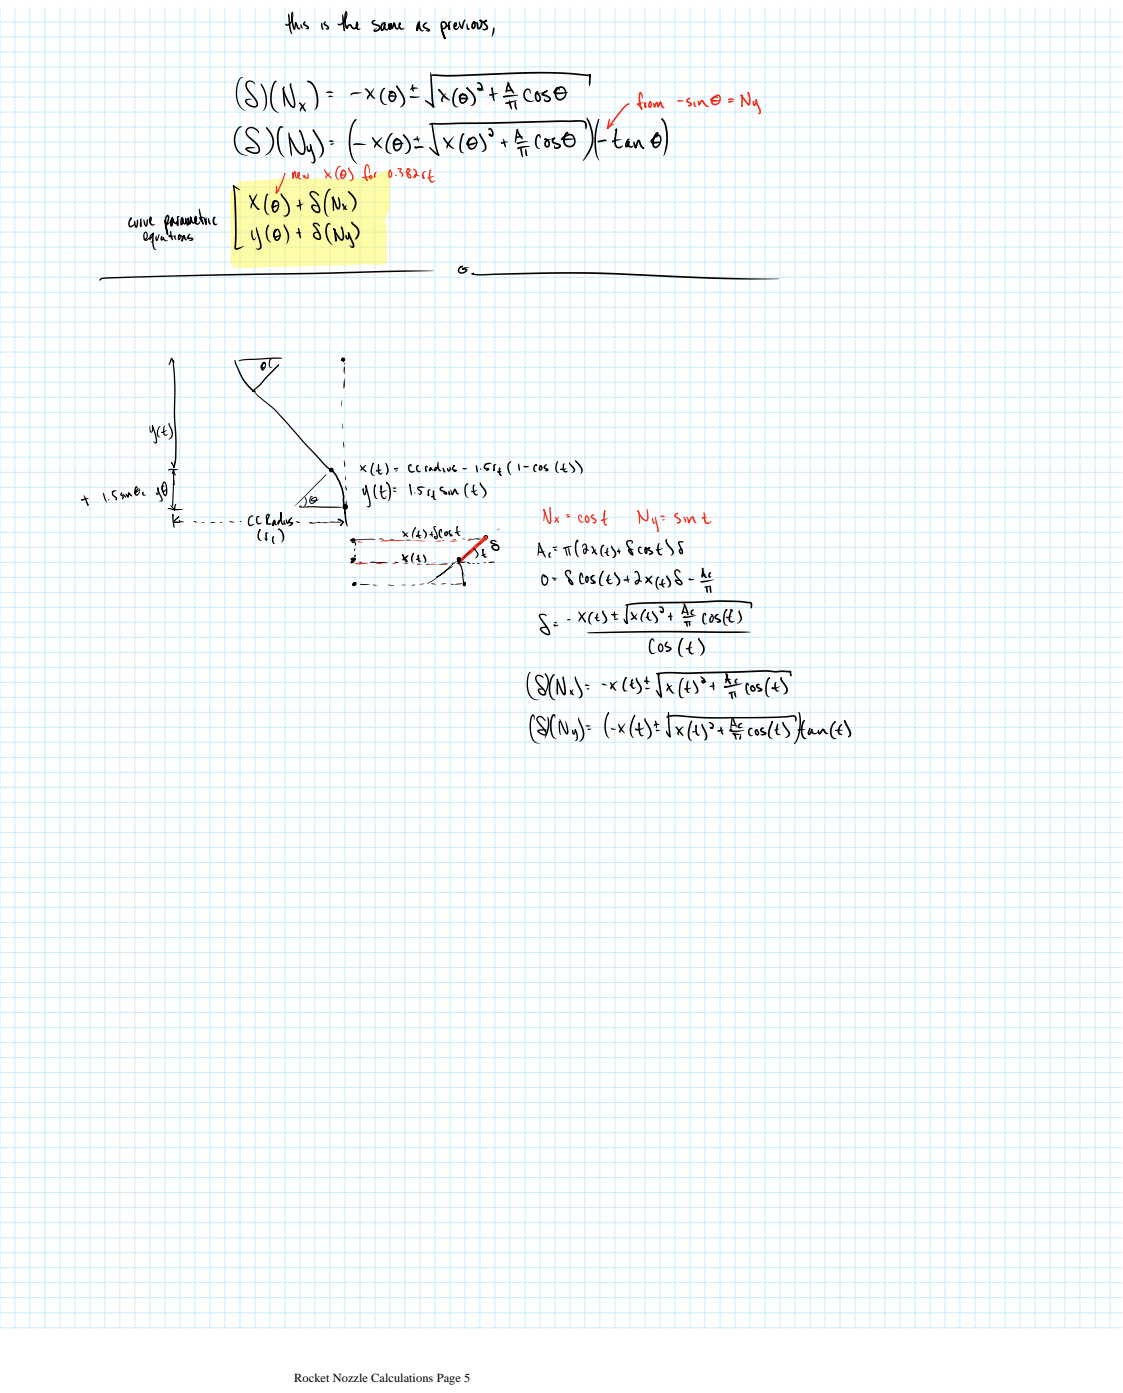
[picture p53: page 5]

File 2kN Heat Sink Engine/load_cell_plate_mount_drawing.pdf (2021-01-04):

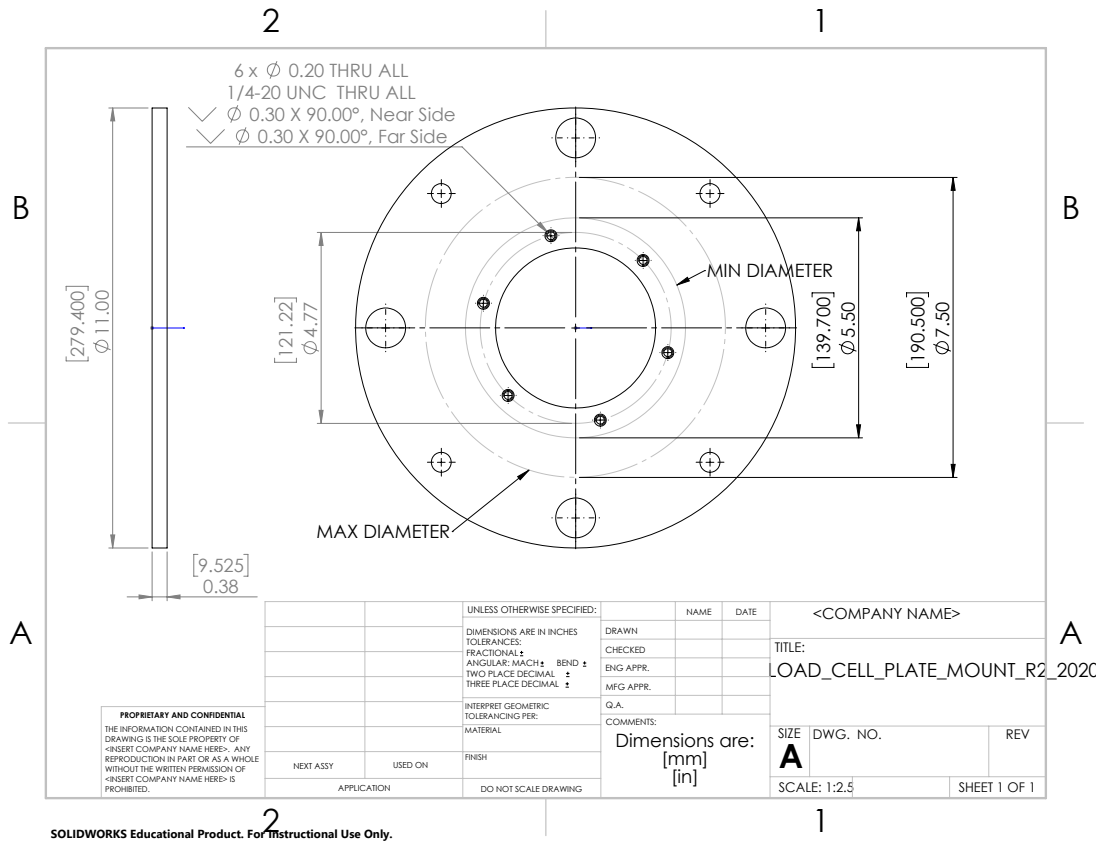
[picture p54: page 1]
0.20 THRU ALL; MAX DIAMETER; MIN DIAMETER; Dimensions are:

1/4-20 UNC THRU ALL
0.30 X 90.00°, Near Side
0.30 X 90.00°, Far Side 121.22 4.77

UNLESS OTHERWISE SPECIFIED: | | NAME | DATE | <COMPANY NAME>
DIMENSIONS ARE IN INCHES TOLERANCES: FRACTIONAL ANGULAR: MACH BEND TWO PLACE DECIMAL THREE PLACE DECIMAL | DRAWN

CHECKED | | | TITLE:

ENG APPR.
MFG APPR.

INTERPRET GEOMETRIC TOLERANCING PER: | Q.A.

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

USED ON | MATERIAL | | SIZE A | DWG. NO. | REV

NEXT ASSY | | FINISH
APPLICATION | DO NOT SCALE DRAWING | | SCALE: 1:2.5 | | SHEET 1 OF 1

SOLIDWORKS Educational Product. For Instructional Use Only.

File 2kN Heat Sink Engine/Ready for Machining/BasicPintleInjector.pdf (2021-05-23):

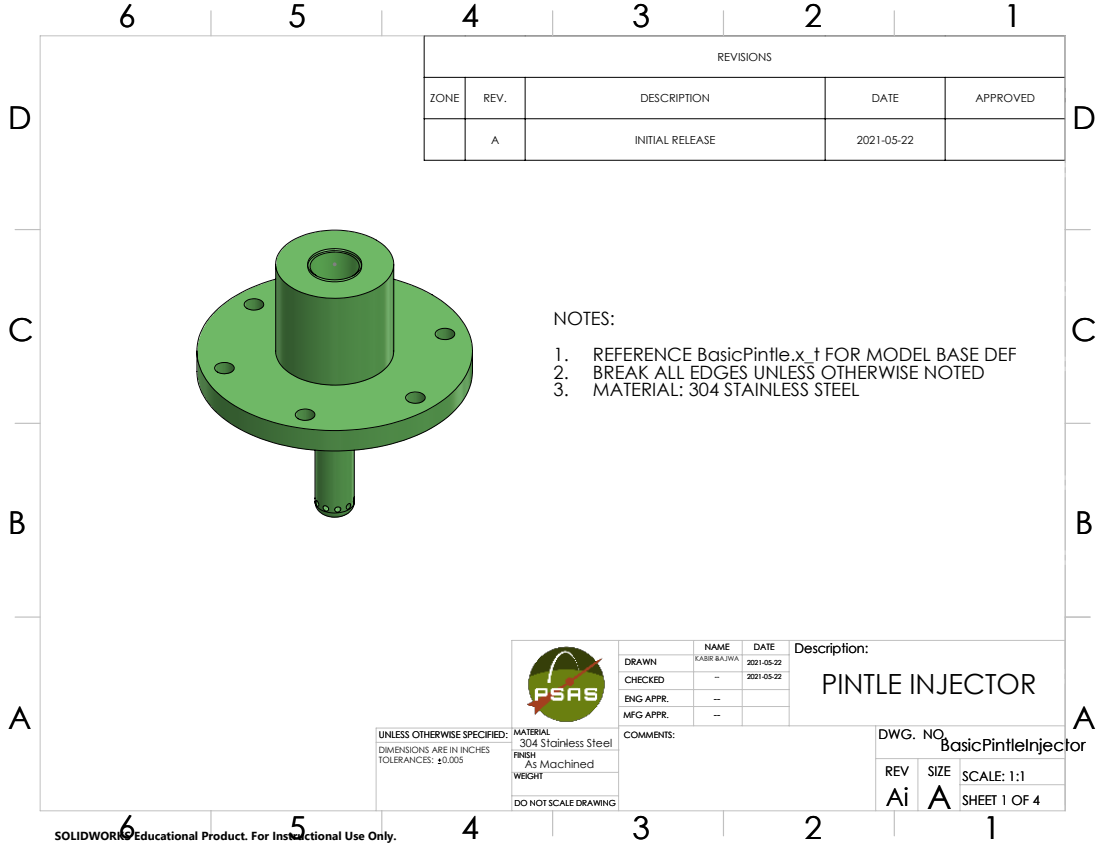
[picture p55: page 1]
REV; SCALE: 1:1; DO NOT SCALE DRAWING; SHEET 1 OF 4; As Machined

REVISIONS

ZONE | REV. | DESCRIPTION | DATE | APPROVED

A | INITIAL RELEASE | 2021-05-22

NOTES:
1. REFERENCE BasicPintle.x_t FOR MODEL BASE DEF
2. BREAK ALL EDGES UNLESS OTHERWISE NOTED
3. MATERIAL: 304 STAINLESS STEEL

NAME | DATE | Description: Description: PINTLE INJECTOR

DRAWN | KABIR BAJWA -- | 2021-05-22
CHECKED | ---- | 2021-05-22
ENG APPR. | ----
MFG APPR. | ----

UNLESS OTHERWISE SPECIFIED: | MATERIAL MATERIAL 304 Stainless Steel - | COMMENTS: | DWG. NO.

DIMENSIONS ARE IN INCHES
TOLERANCES: 0.005

SOLIDWORKS Educational Product. For Instructional Use Only.

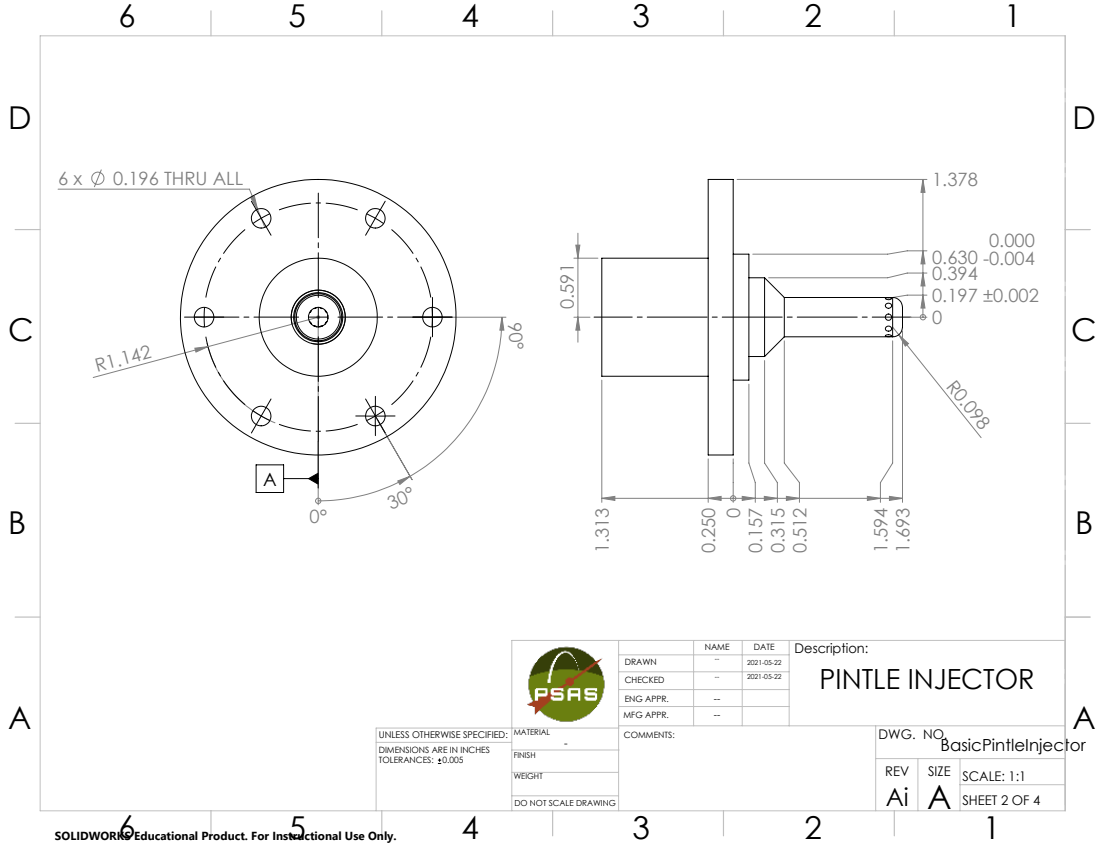
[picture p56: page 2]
0.196 THRU ALL; REV; SCALE: 1:1

NAME | DATE | Description: PINTLE INJECTOR

DRAWN | -- | 2021-05-22
CHECKED | -- | 2021-05-22
ENG APPR. | --
MFG APPR. | --

UNLESS OTHERWISE SPECIFIED: | MATERIAL - | COMMENTS: | DWG. NO.

DIMENSIONS ARE IN INCHES
TOLERANCES: 0.005

0.438 0.672 1/4 NPT 0.542 X 90°, Near Side; SECTION A-A; SCALE 1 : 1; DETAIL D; SCALE 5 : 1; REV; SCALE: 1:1; AS MACHINED

NAME | DATE | Description: PINTLE INJECTOR

DRAWN | KABIR BAJWA | 2021-05-22
CHECKED | -- | 2021-05-22
ENG APPR. | --
MFG APPR. | --

UNLESS OTHERWISE SPECIFIED: | MATERIAL 304 STAINLESS STEEL | COMMENTS: | DWG. NO.

DIMENSIONS ARE IN INCHES
TOLERANCES: 0.005

0.063 THRU ALL; SECTION C-C; SCALE 3 : 1; REV; SCALE: 1:2; AS MACHINED

NAME | DATE | Description: PINTLE INJECTOR

DRAWN | KABIR BAJWA | 2021-05-22
CHECKED | -- | 2021-05-22
ENG APPR. | --
MFG APPR. | --

UNLESS OTHERWISE SPECIFIED: | MATERIAL 304 STAINLESS STEEL | COMMENTS: | DWG. NO.

DIMENSIONS ARE IN INCHES
TOLERANCES: 0.005

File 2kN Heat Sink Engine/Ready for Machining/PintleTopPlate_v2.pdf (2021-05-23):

REV; SCALE: 1:2; DO NOT SCALE DRAWING; SHEET 1 OF 4; As Machined

REVISIONS

ZONE | REV. | DESCRIPTION | DATE | APPROVED

A | INTIAL RELEASE | 2021-05-22

NOTES:
1. REFERENCE PintleTopPlate.x_t FOR MODEL BASE DEF
2. BREAK ALL EDGES UNLESS OTHERWISE NOTED
3. MATERIAL: 304 STAINLESS STEEL

NAME | DATE | Description: Pintle Top Plate

DRAWN | KABIR BAJWA | 2021-05-22
CHECKED | -- | 2021-05-22
ENG APPR. | --
MFG APPR. | --

UNLESS OTHERWISE SPECIFIED: | MATERIAL 304 Stainless Steel | COMMENTS: | DWG. NO. PintleTopPlate

DIMENSIONS ARE IN INCHES
TOLERANCES: 0.005
UNLESS OTHERWISE NOTED

SOLIDWORKS Educational Product. For Instructional Use Only.

10-24 UNC; 0.196 THRU ALL; 0.012 X 45° DETAIL A; SCALE 6 : 1; REV; SCALE: 1:2; As Machined

NAME | DATE | Description: Pintle Top Plate

DRAWN | KABIR BAJWA | 2021-05-22

ENG APPR. | --
MFG APPR. | --

UNLESS OTHERWISE SPECIFIED: | MATERIAL 304 Stainless Steel | COMMENTS: | DWG. NO. PintleTopPlate

DIMENSIONS ARE IN INCHES
TOLERANCES: 0.005
UNLESS OTHERWISE NOTED

1/4 NPT 0.510 X 90°, Near Side; SECTION B-B; REV; SCALE: 1:2; As Machined

(CIRCUMFERENCE TO CENTER)

NAME | DATE | Description: Pintle Top Plate

DRAWN | KABIR BAJWA | 2021-05-22
CHECKED | -- | 2021-05-22
ENG APPR. | --
MFG APPR. | --

UNLESS OTHERWISE SPECIFIED: | MATERIAL 304 Stainless Steel | COMMENTS: | DWG. NO. PintleTopPlate

DIMENSIONS ARE IN INCHES
TOLERANCES: 0.005
UNLESS OTHERWISE NOTED

SECTION C-C; DETAIL D; SCALE 3 : 1; DETAIL G; SCALE 1 : 1; REV; SCALE: 1:2; As Machined

NAME | DATE | Description: Pintle Top Plate

DRAWN | KABIR BAJWA | 2021-05-22
CHECKED | -- | 2021-05-22
ENG APPR. | --
MFG APPR. | --

UNLESS OTHERWISE SPECIFIED: | MATERIAL 304 Stainless Steel | COMMENTS: | DWG. NO. PintleTopPlate

DIMENSIONS ARE IN INCHES
TOLERANCES: 0.005
UNLESS OTHERWISE NOTED

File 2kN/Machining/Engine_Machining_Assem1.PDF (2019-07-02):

6x holes for #10-32 all thread Order 4ft; 1/4in bolt

Three sq. tubes
ST 304 TUBE SQUARE
Order 2ft

TOLERANCES: FRACTIONAL ANGULAR: MACH BEND TWO PLACE DECIMAL THREE PLACE DECIMAL | | NAME | DATE DIMENSIONS ARE IN INCHES

DRAWN
CHECKED
ENG APPR.

PROPRIETARY AND CONFIDENTIAL THE INFORMATION CONTAINED IN THIS DRAWING IS THE SOLE PROPERTY OF <COMPANY NAME >. ANY REPRODUCTION IN PART OR AS A WHOLE WITHOUT THE WRITTEN PERMISSION OF <COMPANY NAME> IS PROHIBITED. | | | MFG APPR.

MATERIAL | Q.A.

NEXT ASSY | USED ON | FINISH

SIZE A | DWG. NO. Engine Fixture | REV.

APPLICATION | | DO NOT SCALE DRAWING

SCALE:1:2 | WEIGHT: | SHEET 1 OF 1

SOLIDWORKS Educational Product. For Instructional Use Only.

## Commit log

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2016-04-07 fixing linear contraction para cooling outer
2016-04-07 fixing cooling channel outer para equations
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2016-05-17 Fixed inner velocites and areas
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2019-09-06 Delete Fixture.SLDPRT
    Removing for incorrect dimensions. Uploading correct one from post-machining.
    [Fixture.SLDPRT]
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2019-12-24 Added V3 folder
    Added V3 folder. Made a few small changes to V2 first
    [5482K113_PRECISION AN 37 DEGREE FLARED TUBE FITTING.SLDPRT, 5482K210_PRECISION AN 37 DEGREE FLARED TUBE FITTING.SLDPRT, 90037A112_METRIC HIGH-STRENGTH 316 SS S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]
2019-12-24 created V4
    got an idea to make things simpler and made another assembly. premature to call it V4 and maybe don't need to be creating a whole new folder but whatever
    [5482K113_PRECISION AN 37 DEGREE FLARED TUBE FITTING.SLDPRT, 5482K210_PRECISION AN 37 DEGREE FLARED TUBE FITTING.SLDPRT, 90037A112_METRIC HIGH-STRENGTH 316 SS S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]
2020-01-07 created V5 with changes from review 1/7
    see 2019-2020 LFE/LFETS Notes in PSAS google drive for review notes
    [5482K113_PRECISION AN 37 DEGREE FLARED TUBE FITTING.SLDPRT, 5482K210_PRECISION AN 37 DEGREE FLARED TUBE FITTING.SLDPRT, 90037A112_METRIC HIGH-STRENGTH 316 SS S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]
2020-01-07 V5 created w V3 and V4 LOX configs
    V3 and V4 configurations for alternate LOX connection
    [LOXAdapterV4.SLDPRT, LogRocketV3.SLDASM, LogRocketV5.SLDASM]
2020-01-08 fixed error in SolidRocket sketch
    That's why the bolt pattern was weird
    [InjectorBaseV5.SLDPRT, InjectorCapV5.SLDPRT, LogRocketV5.SLDASM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]
2020-01-08 added seal grooves
    added seal grooves and linked depth to global variable in LogRocketV5 assembly
    [InjectorBaseV5.SLDPRT, InjectorCapV5.SLDPRT, LOXAdapterOnePieceV5.SLDPRT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]
2020-01-08 try that again with SW closed
    not sure if GitHub pushes all the temporary SW files if commit while SW open
    [LogRocketV5.SLDASM, SolidRocket.SLDDRW]
2020-01-08 thickened baffles
    also added V6 idea for pintle head, currently suppressed. fuel from sides instead of top
    [InjectorBaseV5.SLDPRT, LOXAdapterOnePieceV5.SLDPRT, LOXAdapterV3.SLDPRT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]
2020-01-15 V6 version added
    created V6 version w/ two-piece combustion chamber/nozzle. still need to smooth fluid flow geometry
    [InjectorBaseV5.SLDPRT, InjectorCapV5.SLDPRT, LOXAdapterOnePieceV5.SLDPRT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]
2020-01-17 alternate LOX input in V5
    trying out LOX in from sides rather than top
    [InjectorBaseV5.SLDPRT, LOXAdapterOnePieceV5.SLDPRT, LOXAdapterOnePieceV6.SLDPRT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]
2020-01-17 started fixing bunch of crap in V5
    little things like assembly hierarchy, part orientation, mating planes and not faces. V5 is still basis for current design
    [Engine_body.sldasm, InjectorBaseV5.SLDPRT, InjectorCapV5.SLDPRT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]
2020-01-22 big update
    new V6_B pintle design. added fasteners. still need to redo orifice dimensions. need to add grooves again. need to verify nipple/fitting sizes
    [5482K113_PRECISION AN 37 DEGREE FLARED TUBE FITTING.SLDPRT, 5482K150_PRECISION AN 37 DEGREE FLARED TUBE FITTING.SLDPRT, 92196A332_18-8 STAINLESS STEEL SOCKET H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]
2020-01-24 updated pintle dims. created load cell assy
    brought in load cell assy from test stand cad to check fit. routing hoses/tubing will be tricky
    [F1495P.SLDPRT, InjectorBaseV6.SLDPRT, LogRocketV6.SLDASM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]
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2020-01-30 modeling tubing routing
    added load cell, modeled load cell to test stand frame adapter. modified load cell test stand-side plate to accomodate LOX hard tubing.
    [25NPTto38tubingOD.SLDASM, 38minL.SLDPRT, 50715K318_TYPE 316 SS 37 DEGREE FLARED TUBE FITTING.SLDPRT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]
2020-01-31 moved star files out - very large
    Due to file sizes, I will be more judicious with simulation files in repo.
    [PintleV6_forstar.SLDASM, PintleV6_forstar.x_t]
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2020-02-11 created solid single part rocket body
    starting point for additive manufacturing design
    [PintleV6.SLDASM, Pintle_OuterV6.SLDPRT, RocketBodyV6.sldasm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]
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2020-02-12 pintle fever
    trying out more more more pintles in the design for printing
    [25NPTto38tubingOD.SLDASM, 38minL.SLDPRT, 50715K318_TYPE 316 SS 37 DEGREE FLARED TUBE FITTING.SLDPRT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]
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2020-02-16 work work work
    still need to add pressure transmitter boss/NPT hole, save test.sldasm into part and combine bodies. change pintle thread to straight thread. re-model machined design
    [ipa-support.sldprt]
2020-02-17 ready for review
    did everything I could think of to rocket engine body (too much), except for pintle
    [beehive3.SLDPRT, ipa-support.sldprt]
2020-02-18 pintle work
    made new pintle and put in McMaster crush washers. will they work?
    [97725A123_METAL SEALING WASHER.SLDPRT, 97725A590_METAL SEALING WASHER.SLDPRT, NozzleProfile_Smaller.SLDPRT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]
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2020-03-05 made 285 mm tall engine for 3DLogics
    made 285 mm tall engine for 3DLogics
    [5482K124_PRECISION AN 37 DEGREE FLARED TUBE FITTING.SLDPRT, drilling-pintle.SLDPRT, ipa-support.sldprt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]
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2020-03-06 pintle changes
    reflecting initial pressure drop measurement project. holes changed to #56 (.0465 in). length of pintle changed for 1:1 skip distance to pintle OD
    [pintleV7-4.sldasm, pintleV7-5.SLDASM, pintleV7-5.SLDPRT]
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2020-04-09 work during zoom meeting
    closer. need to finish 6x mounting screw area, rough in gasketed joint
    [HYBRID_MASTER.SLDASM, chamber.sldprt, injectorHead.sldprt]
2020-04-16 progress on injector head
    still to do:
    spec main seal/groove
    check bolt pattern sufficient for seal and compression/preload
    other stuff
    [91950A029_TYPE 316 STAINLESS STEEL SAE FLAT WASHER.SLDPRT, 92196A329_18-8 STAINLESS STEEL SOCKET HEAD CAP SCREW.SLDPRT, 92673A116_ASTM F594 TYPE 18-8 STAINLESS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]
2020-04-22 re-exported parasolid files for RFQ from 3D logics
    had to export a parasolid, import back into SW, fix faulty faces, then re-export
    [HYBRID_MASTER.SLDASM, injectorHead.x_t, injectorHead_repaired.SLDPRT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]
2020-05-07 got rid of sw modeled npt tapped holes for fuel
    maybe make them bigger though?
    [5482K126_PRECISION AN 37 DEGREE FLARED TUBE FITTING.SLDPRT, 92196A311_18-8 STAINLESS STEEL SOCKET HEAD CAP SCREW.SLDPRT, HYBRID_MASTER.SLDASM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]
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2021-03-05 Fixed wrong number of mounting holes and changed units in drawing to in.
    [ThroatlessEngine.SLDPRT, ThroatlessEngineBasePlate.SLDDRW, ThroatlessEngineBasePlate.SLDPRT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]
2021-03-24 Changed hole size and tube tolerance
    [ThroatlessEngine.SLDPRT, ThroatlessEngineBasePlate.SLDDRW, ThroatlessEngineBasePlate.SLDPRT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]
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2021-04-03 Revert "Refined flow sim"
    This reverts commit efad51127dbe229ab1bb18ad1de7e9a9b28a0be1.
    [FullStack.SLDASM, LID22.SLDPRT, LID23.SLDPRT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]
2021-04-03 Worked on flow sim parametric study, still buggy
    [FullStack.SLDASM, LID22.SLDPRT, Pintle.SLDPRT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]
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2021-05-20 Updated sims, fixed folder name
    [CopSubReplica.SLDPRT, ThroatlessEngine.SLDPRT, ThroatlessEngineBasePlate.SLDDRW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]
2021-05-20 Fixed names, changed formats
    [8 kN_flight_engine.cfg, 8 kN_flight_engine_rad+film.cfg, 8 kN_flight_engine_regen+film+rad_nozzle.cfg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]
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
